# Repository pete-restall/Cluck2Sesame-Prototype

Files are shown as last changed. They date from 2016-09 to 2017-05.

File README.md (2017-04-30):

# Cluck<sup>2</sup>Sesame - Yet Another Chicken Coop Door Opener

## What is it ?
It opens and closes the door of my wife's chicken coop based on Sunrise and
Sunset times so that she doesn't have to.  Or rather, it will do when I get
the time to finish it between paid work and free time.

## Why 'Cluck<sup>2</sup>Sesame' ?
Because 'Cluck Cluck Sesame' is obviously what the chickens would say if
they needed to open a door.  And 'Chicken Sesame' is a recipe.

## The Hardware and Firmware
The hardware and firmware are all mine.  The board is based around a
[PIC16F685](doc/datasheets/mcu/PIC16F685-I.pdf) as I've had some lying around
for years and was looking for an excuse to use them up.

The PIC16F685 is an 8-bit microcontroller with a whopping 4K of program words
(flash) and 256 bytes of RAM that can run at a respectable 8MHz (2MIPS)
without an external clock.  But more importantly it's got excellent
power-saving capabilities, which is critical when running off batteries.
Being a PIC it's also got a brilliant array of peripherals and an adequate
20-pin package.

The firmware is an experiment in writing test-first assembler, an endeavour
somewhat trickier than with high-level counterparts due to its lack of
encapsulation, global state, side-effects, the vagaries of linking, as well
as the verbosity of the language.  The tests are run in gpsim with bash
scripts for glue.  They are run as part of the automated Travis build.

## Pictures
| Freshly baked and stuffed PCB         | Attached to the Coop                        |
----------------------------------------|----------------------------------------------
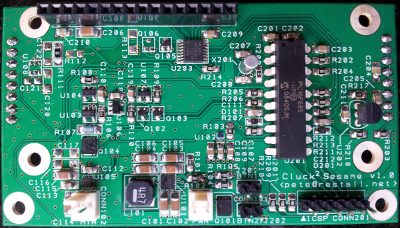
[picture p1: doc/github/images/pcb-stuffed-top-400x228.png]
Stuffed PCB
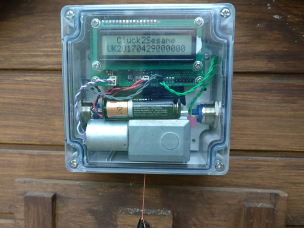
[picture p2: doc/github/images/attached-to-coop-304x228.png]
Attached to Coop
|  |  |

## Build


[stuffed-pcb-top-small]: doc/github/images/pcb-stuffed-top-400x228.png "Stuffed PCB (top)"
[attached-to-coop-small]: doc/github/images/attached-to-coop-304x228.png "Attached to Coop"

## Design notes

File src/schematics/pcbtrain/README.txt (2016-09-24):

Customer:
---------
Pete Restall (Parity Computer Consultancy Limited) - pete@restall.net
Any problems / questions, please do not hesitate to get in touch.

Guidelines Followed From:
-------------------------
http://www.pcbtrain.co.uk/schematic/pcb-technical-advice/

Design Tools Used:
------------------
DesignSpark 7.1
GC-Prevue 24.3.8

Track and Spacing:
------------------
Minimum 6mil.

Layers:
-------
All viewed from above, no mirroring.  Solder Resist layers are negatives, all
others are positives.  See "Cluck2Sesame Layers.pdf" for a non-Gerber
representation of what the individual layers should look like.

Board Outline:
--------------
All layers contain a zero-width board outline.  Outline size is
3.542in x 1.968in and >= 10mil from any feature, copper or otherwise.

Vias and Silkscreen:
--------------------
Some vias are partially covered with silkscreen; this is not anticipated to
be an issue since they should be covered / plugged with resist.

Pads and Silkscreen:
--------------------
CONN204 silkscreen touches the M3 washer pad in the top-left of the board but
should not cover it.  The silkscreen can be clipped where necessary, but
please advise if this is going to be an issue.

Vias and Pads:
--------------
Some vias are very close to pads, but the outer edge of drill holes should
be >= 6mil from the edge of the pad.  This may or may not be an issue (ie.
solder resist only covering part of a via), but please advise if it will
impact on manufacture.

There are two vias inside the thermal pad of U101.  These are not tented as
they provide thermal relief.  Please advise if this is an issue.

Drill Holes:
------------
All are through-plated and are finished sizes; no adjustments have been made
for plating thickness.  All are >= 10mil from the edge of the board.

Bit sizes can be rounded to the nearest 0.1mm.  Please advise if any drill
sizes are found to be incompatible with your processes.

Annular rings >= 6mil.

Data Formats:
-------------
More detailed information can be found in "DesignSpark Plot Report.TXT", but
in summary:

---------------
Gerber Settings
---------------

    Leading zero suppression.
    G01 assumed throughout.
    Line termination <*> <CR> <LF>.
    3.5 format absolute inches.
    Format commands defined in Gerber file.
    Aperture table defined in Gerber file.
    Hardware arcs allowed.

--------------
Drill Settings
--------------

    Excellon Format 1
    Format 3.5 absolute in inches.
    No zero suppression.

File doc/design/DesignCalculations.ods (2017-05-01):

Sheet: Motor
Lifting a Weight
Weight (kg) | 1
Height (cm) | 40
Time to Raise (s) | 20
Mechanical Power Required (W) | 0.1962
Motor |  |  | Rapid 37-0142 | JGY-370-320
Output Power (W) | 0.56 | Datasheet parameter | 0.56 | 0.45
Current (mA) | 360 | Datasheet parameter | 360 | 230
Angular Speed (rpm) | 5200 | Datasheet parameter | 5200 | 7
Torque (g.cm) | 10.5 | Datasheet parameter | 10.5 | 1000
Efficiency | 51.90% | Datasheet parameter | 51.90% | 30.00%
Input Power (W) | 1.07899807321773 | Worm efficiency will be < 50%, so add a decent margin; also allow higher transient current when starting (overcome worm static friction)
Angular Speed (rads/s) | 544.542726622231
Torque (Nm) | 0.00102969825315
Gears
Worm Gear Reduction (1:N) | 150
Shaft / Pulley Diameter (mm) | 20
Torque of 1kg Weight on Pulley (Nm) | 0.0981
Angular Speed (rpm) | 34.6666666666667
Angular Speed (rads/s) | 3.63028484414821
Torque at Worm Gear (Nm) | 0.1544547379725
Lifting Force (N) | 15.44547379725
Lifting Weight (kg) | 1.57446216077982
Lifting Speed (mm/s) | 36.3028484414821
Time to Raise (s) | 11.0184191371312
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

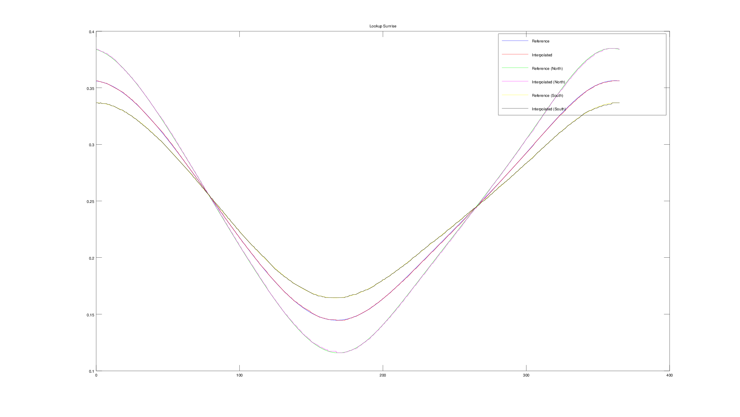
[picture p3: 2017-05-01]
doc/github/images/octave-sunrise-lookup-comparison-1920x1080.png

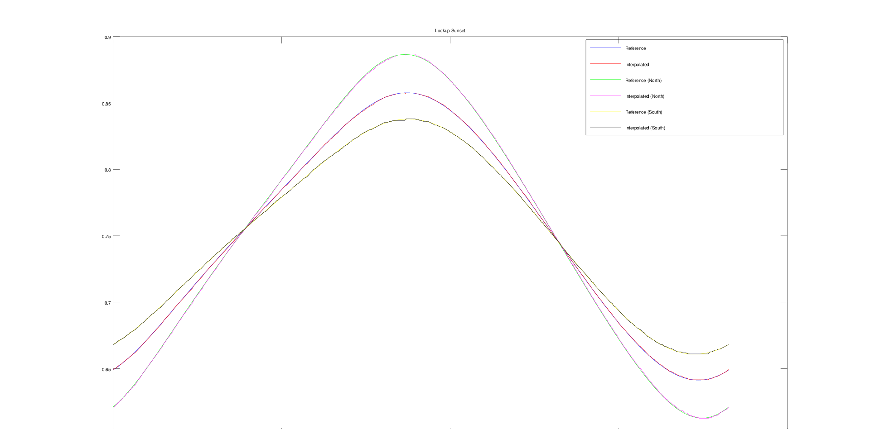
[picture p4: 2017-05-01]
doc/github/images/octave-sunset-lookup-comparison-1920x1080.png

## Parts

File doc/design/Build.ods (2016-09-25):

Item | Quantity Required | Quantity Bought | Total Cost | Cost per Unit
LCD | 1 | 2 | £9.54 | £4.77
Motor (With 1:150 Gearbox) | 1 | 1 | £9.20 | £9.20
PCB | 1 | 2 | £58.09 | £29.05
Paste Stencil | 1 | 1 | £14.34 | £14.34
Enclosure | 1 | 1 | £15.90 | £15.90
Buttons | 2 | 2 | £4.78 | £4.78
AA Battery Holders | 2 | 3 | £1.32 | £0.88
LCD Header (Board) | 1 | 10 | £1.74 | £0.17
LCD Header (LCD) | 1 | 10 | £2.75 | £0.28
Button Headers (Board) | 2 | 10 | £2.22 | £0.44
Button Headers (Cable) | 2 | 10 | £0.98 | £0.20
PIC ICSP Header | 1 | 1 | £0.00 | £0.00 | Off-cut from PCB Header
Power Header (Board) | 1 | 10 | £0.98 | £0.10
Power Header (Cable) | 1 | 10 | £0.54 | £0.05
Motor Header (Board) | 1 | 1 | £0.00 | £0.00 | Same as Button Headers
Motor Header (Cable) | 1 | 1 | £0.00 | £0.00 | Same as Power Header
Daughterboard Header | 2 | 10 | £1.03 | £0.21
 |  |  | £123.41 | £80.36

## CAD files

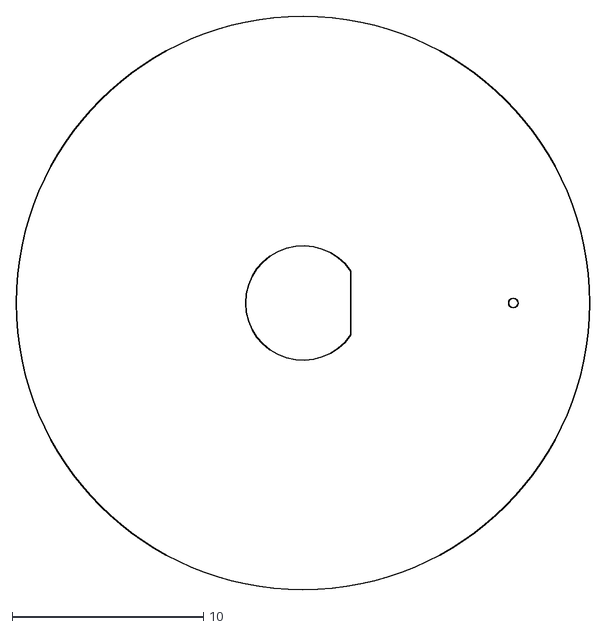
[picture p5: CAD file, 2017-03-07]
src/cnc/Spool/3-Spool.dxf
30.0 x 30.0

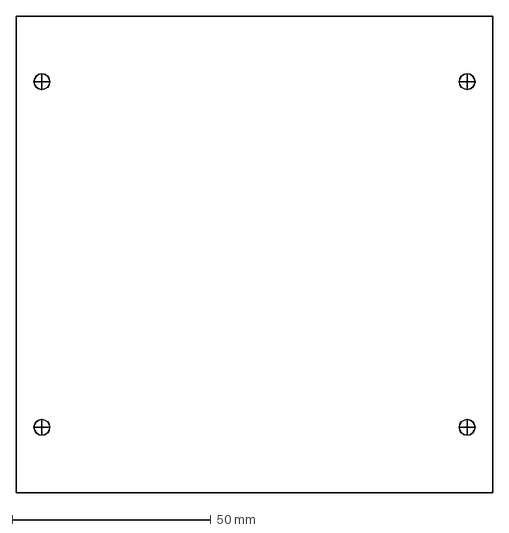
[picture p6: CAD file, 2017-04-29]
src/drawings/MountingHolesTemplate.dxf
120.0 x 120.0 mm

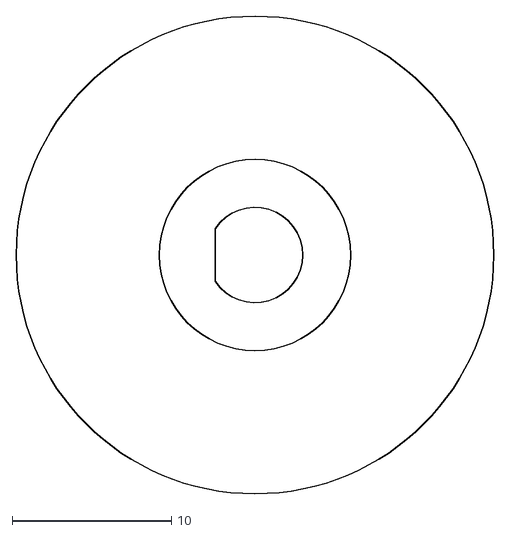
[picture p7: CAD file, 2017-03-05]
src/cnc/Spool/2-Spool.dxf
30.0 x 30.0

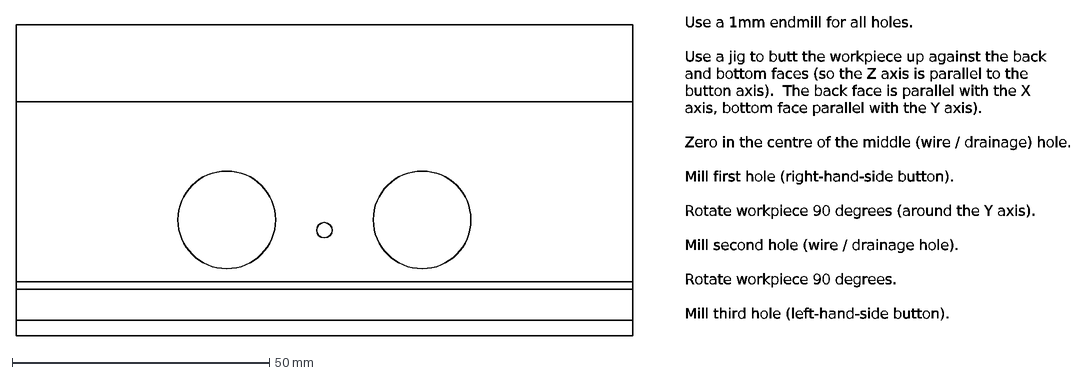
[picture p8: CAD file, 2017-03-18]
src/drawings/Enclosure.dxf
Use a 1mm endmill for all holes. Use a jig to butt the workpiece up against the back and bottom faces (so the Z axis is parallel to the button axis). The back f

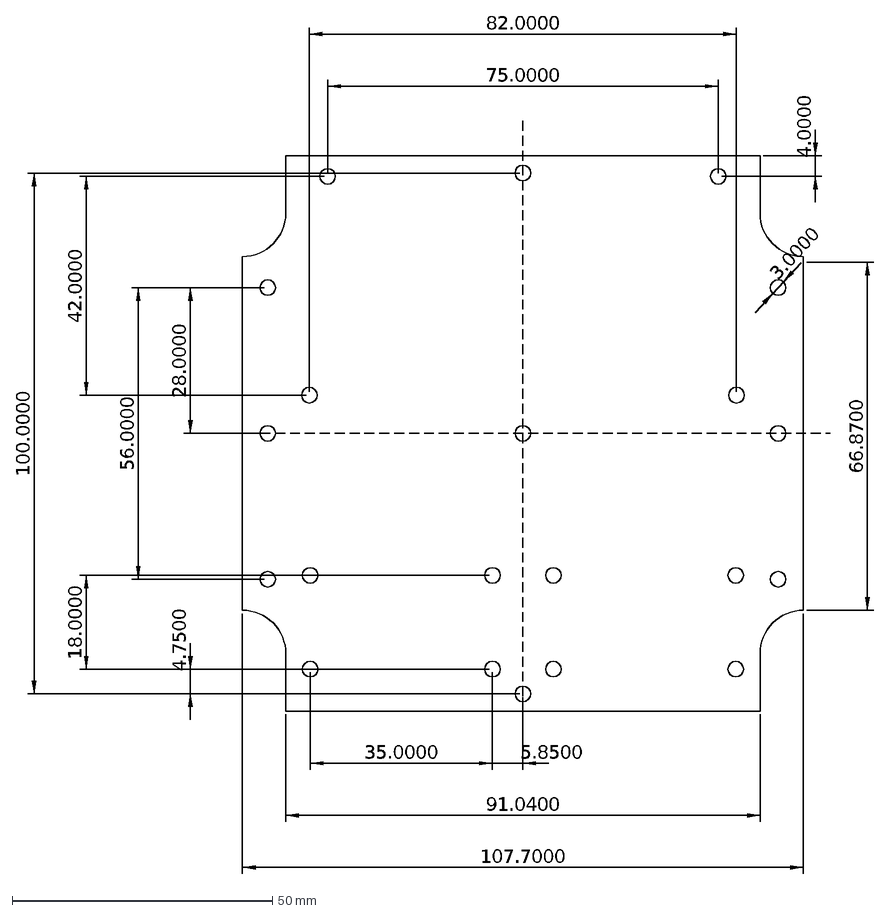
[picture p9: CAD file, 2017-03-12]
src/drawings/BackPlate.dxf
82.0000
4.0000
75.0000
3.0000
66.8700
28.0000
56.0000
42.0000
100.0000
107.7000
91.0400
5.8500
4.7500
18.0000
35.0000

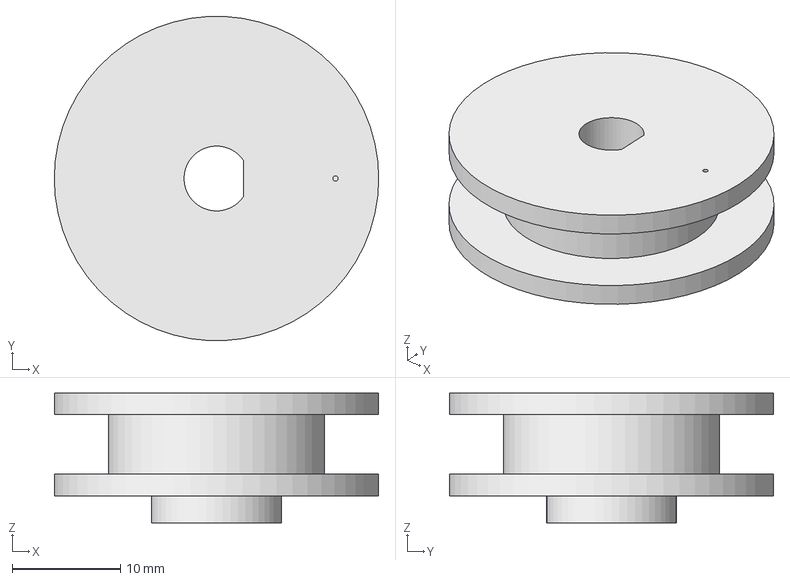
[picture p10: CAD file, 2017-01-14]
src/drawings/Spool.FCStd
30.0 x 30.0 x 12.0 mm

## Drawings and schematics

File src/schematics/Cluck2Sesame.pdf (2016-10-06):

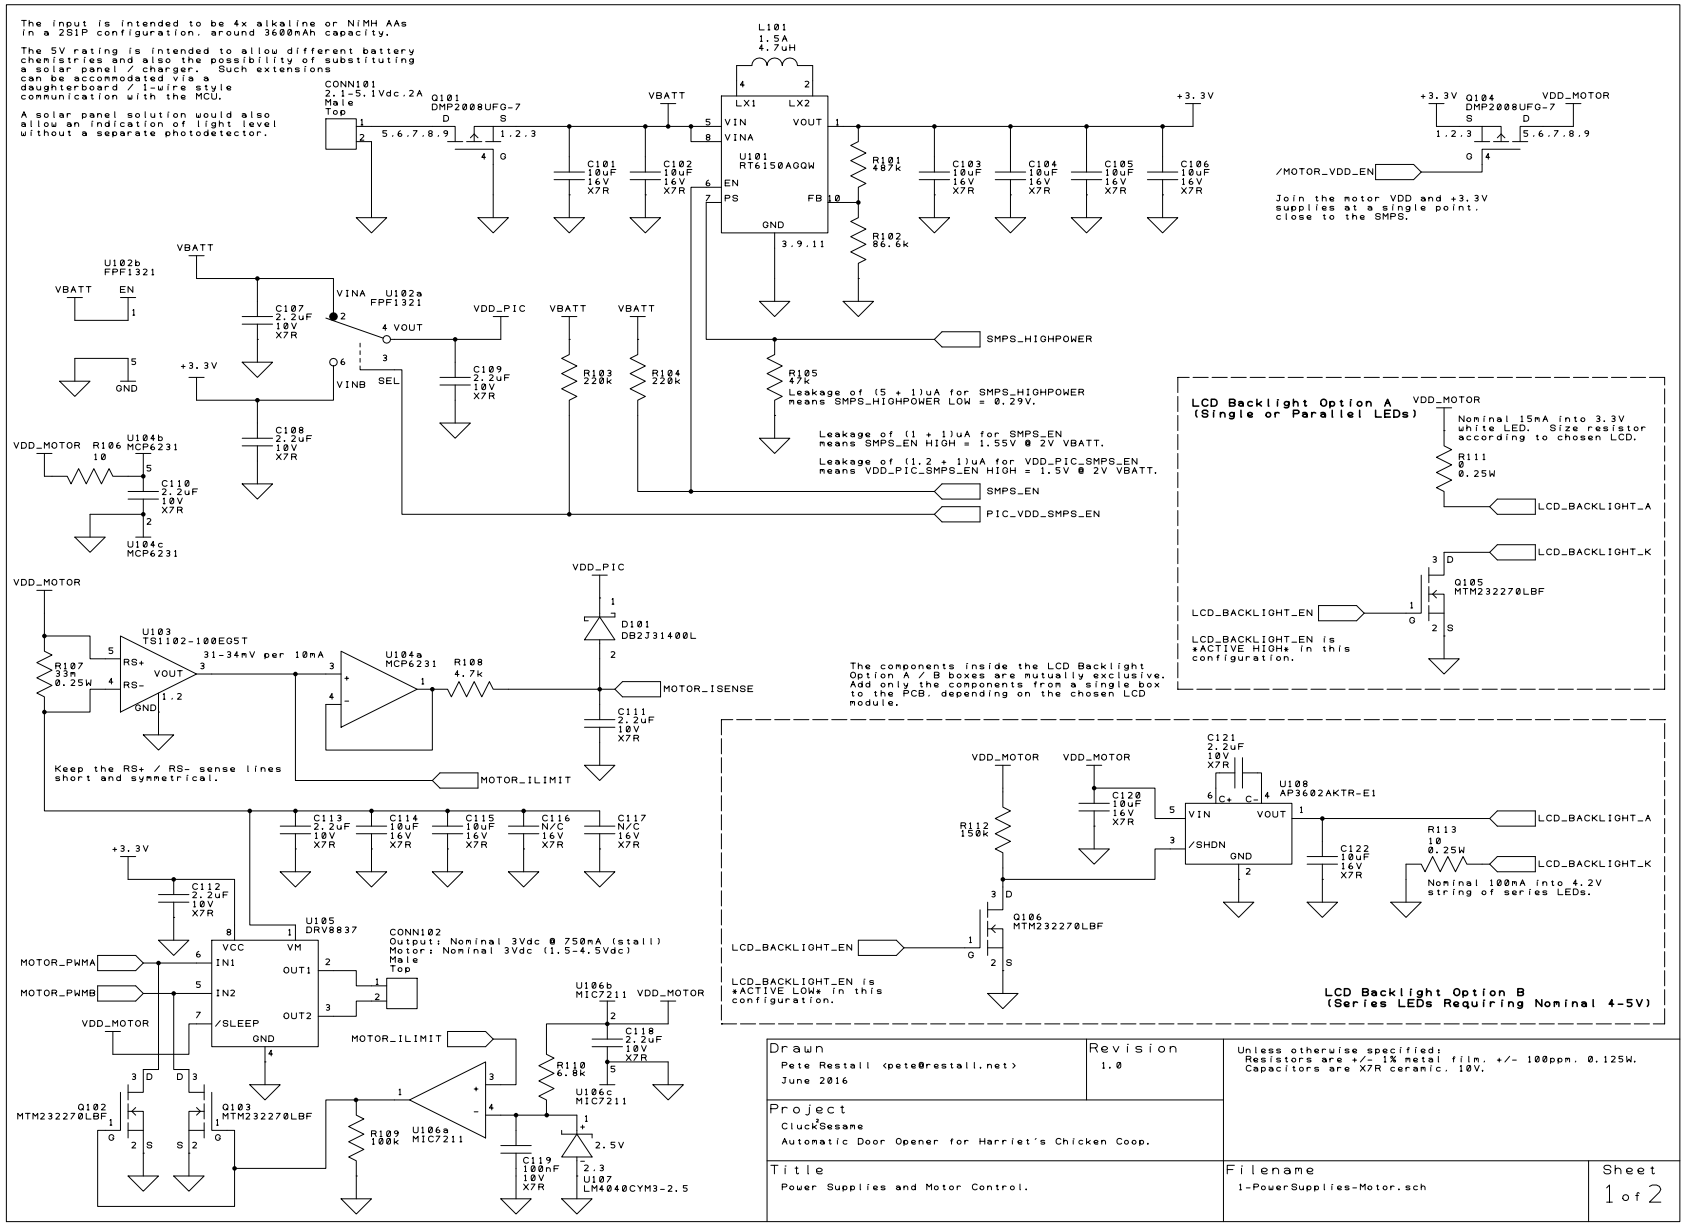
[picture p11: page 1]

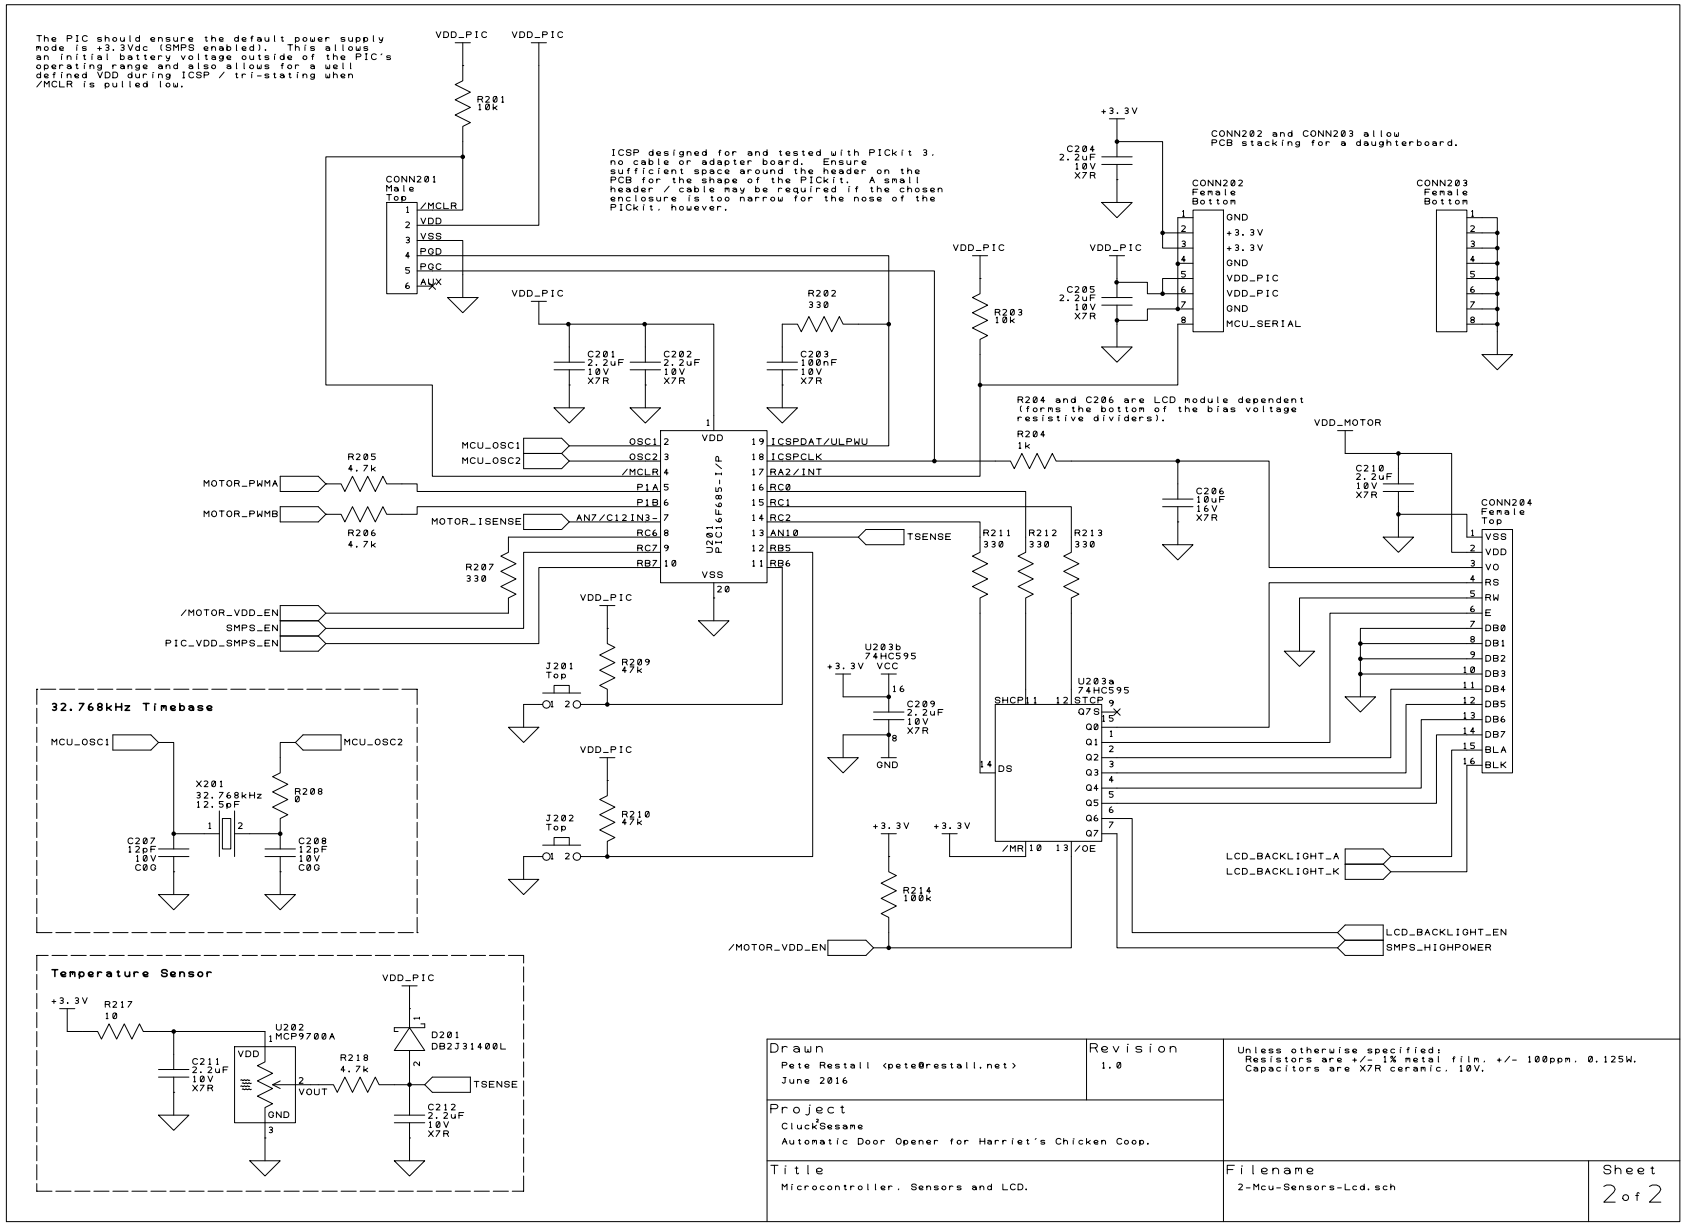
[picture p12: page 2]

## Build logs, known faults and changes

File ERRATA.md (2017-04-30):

# Cluck<sup>2</sup>Sesame - Yet Another Chicken Coop Door Opener
# Errata, Suggested Improvements and Otherwise Undocumented Design Changes

## PCB
- After testing with the actual motor, the LM4040CYM3-2.5 would be best
  replaced with a reference of 2V (or 2.048V for another LM4040 series) for
  a cut-off of about 600mA; the firmware cut-off is about 500mA.  Don't forget
  to re-calculate R110 for the new quiescent current !

- The PIC16F685 was really the wrong choice for this application, but it was
  chosen because it was lying around.  More program space would have eased
  the firmware constraints.  More pins would have allowed the shift register
  to be removed.

## Spool
- The tie-hole on the spool was increased from 0.5mm to 0.8mm to accomodate
  the multi-stranded line.  Multi-stranded line has less stretch and is a
  better fit for this application.

- The height of the stand-off for the spool was decreased as the width of the
  winding section was increased to 5mm.

## Motor
- The JGY-370 is a 6V motor running at around 3V.  While it is sufficient to
  raise and lower a door of about 500g, it wouldn't cope particularly well
  with the 1kg load that was the initial target weight.  Indeed, the current
  cut-off kicks in well before 1kg.

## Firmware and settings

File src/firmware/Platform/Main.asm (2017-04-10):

	#include "Platform.inc"
	#include "FarCalls.inc"
	#include "PowerOnReset.inc"
	#include "BrownOutReset.inc"
	#include "MclrReset.inc"
	#include "PowerManagement.inc"

	radix decimal

	extern pollForWork

Main code
	global main
	global initialisationCompleted

main:
	.safelySetBankFor PCON
	btfss PCON, NOT_POR
	goto powerOnReset
	btfss PCON, NOT_BOR
	goto brownOutReset

mclrReset:
	fcall initialiseAfterMclrReset
	goto pollingLoop

powerOnReset:
	fcall initialiseAfterPowerOnReset
	goto pollingLoop

brownOutReset:
	fcall initialiseAfterBrownOutReset

pollingLoop:
	fcall pollForWork
	goto pollingLoop

initialisationCompleted:
	.safelySetBankFor INTCON
	movlw (1 << GIE) | (1 << PEIE)
	iorwf INTCON

	fcall preventSleep
	fcall pollForWork
	fcall allowSlowClock
	return

	end

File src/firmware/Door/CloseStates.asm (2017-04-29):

	#include "Platform.inc"
	#include "FarCalls.inc"
	#include "Timer0.inc"
	#include "Motor.inc"
	#include "Door.inc"
	#include "States.inc"

	radix decimal

NUMBER_OF_TICKS_0_5S equ 2
NUMBER_OF_TICKS_5S equ 19
NUMBER_OF_TICKS_6S equ 23

	defineDoorState DOOR_STATE_CLOSE
		setDoorState DOOR_STATE_MOTORVDD_ENABLE
		setDoorNextState DOOR_STATE_CLOSE_MOTORVDDENABLED
		returnFromDoorState


	defineDoorStateInSameSection DOOR_STATE_CLOSE_MOTORVDDENABLED
		storeSlowTimer0 doorOperationStartedTimestamp

startLowering:
		.unknownBank
		setDoorState DOOR_STATE_MOTOR_STARTLOWERING
		setDoorNextState DOOR_STATE_CLOSE_LOWERING
		returnFromDoorState


	defineDoorStateInSameSection DOOR_STATE_CLOSE_LOWERING
		; TODO: OVERLOAD - FAULT
		; TODO: TIMEOUT - FAULT
		elapsedSinceSlowTimer0 doorTurnFullSpeedTimestamp
		sublw NUMBER_OF_TICKS_5S
		btfsc STATUS, C
		returnFromDoorState

rewindToTestMotorLoad:
		setDoorState DOOR_STATE_MOTOR_STARTRAISING
		setDoorNextState DOOR_STATE_CLOSE_RAISING
		returnFromDoorState


	defineDoorStateInSameSection DOOR_STATE_CLOSE_RAISING
		; TODO: OVERLOAD - FAULT
		; TODO: TIMEOUT - FAULT
		elapsedSinceSlowTimer0 doorTurnFullSpeedTimestamp
		sublw NUMBER_OF_TICKS_0_5S
		btfsc STATUS, C
		returnFromDoorState

ifMotorLoadPresentThenMoreLoweringIsRequired:
		.setBankFor motorFlags
		btfss motorFlags, MOTOR_FLAG_NOLOAD
		goto startLowering

loweredTooFar:
		bsf motorFlags, MOTOR_FLAG_PREVENT_NOMINALLOAD
		setDoorState DOOR_STATE_CLOSE_WAITFORISRSTOP
		returnFromDoorState


	defineDoorStateInSameSection DOOR_STATE_CLOSE_WAITFORISRSTOP
		.setBankFor PSTRCON
		movlw MOTOR_PSTRCON_OUTPUT_MASK
		andwf PSTRCON, W
		btfsc STATUS, Z
		goto motorStoppedByIsr

motorShouldNotRaiseMuchMoreThanItLowered:
		elapsedSinceSlowTimer0 doorTurnFullSpeedTimestamp
		sublw NUMBER_OF_TICKS_6S
		btfsc STATUS, C
		returnFromDoorState

		; TODO: TIMED OUT WHILE WAITING FOR LOAD TO BITE - FAULT

motorStoppedByIsr:
		.safelySetBankFor motorFlags
		bcf motorFlags, MOTOR_FLAG_PREVENT_NOMINALLOAD
		setDoorState DOOR_STATE_MOTOR_DONE
		setDoorNextState DOOR_STATE_CLOSED
		returnFromDoorState


	defineDoorStateInSameSection DOOR_STATE_CLOSED
		bsf doorFlags, DOOR_FLAG_CLOSED
		bcf doorFlags, DOOR_FLAG_OPENED
		setDoorState DOOR_STATE_WAIT_NEWDAY
		returnFromDoorState

	end

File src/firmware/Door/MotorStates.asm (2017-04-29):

	#include "Platform.inc"
	#include "FarCalls.inc"
	#include "Timer0.inc"
	#include "PowerManagement.inc"
	#include "Motor.inc"
	#include "Door.inc"
	#include "States.inc"

	radix decimal

	defineDoorState DOOR_STATE_MOTOR_STARTRAISING
		fcall turnMotorClockwise
		goto afterCallToTurn

	defineDoorStateInSameSection DOOR_STATE_MOTOR_STARTLOWERING
		fcall turnMotorAntiClockwise

afterCallToTurn:
		.unknownBank
		xorlw 0
		btfsc STATUS, Z
		returnFromDoorState

		storeSlowTimer0 doorTurnStartedTimestamp
		setDoorState DOOR_STATE_MOTOR_WAITFULLYTURNING
		returnFromDoorState


	defineDoorStateInSameSection DOOR_STATE_MOTOR_WAITFULLYTURNING
		fcall isMotorFullyTurning
		xorlw 0
		btfsc STATUS, Z
		returnFromDoorState

		storeSlowTimer0 doorTurnFullSpeedTimestamp

		.setBankFor doorNextState
		movf doorNextState, W
		movwf doorState
		returnFromDoorState


	defineDoorStateInSameSection DOOR_STATE_MOTOR_DONE
		fcall stopMotor
		setDoorState DOOR_STATE_MOTOR_WAITSTOP
		returnFromDoorState


	defineDoorStateInSameSection DOOR_STATE_MOTOR_WAITSTOP
		.setBankFor CCPR1L
		movf CCPR1L
		btfss STATUS, Z
		returnFromDoorState

		.setBankFor doorNextState
		movf doorNextState, W
		movwf doorState

		fcall disableMotorVdd
		fcall preventSleep
		returnFromDoorState

	end

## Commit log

2016-06-24 Initial commit.
    [1-PowerSupply.sch, 2-Microcontroller.sch, DesignCalculations.ods]
2016-06-24 The beginnings of an MCU schematic.
    [1-PowerSupply.sch, 2-Microcontroller.sch, DesignCalculations.ods]
2016-06-25 More work on the microcontroller schematics.
    [1-PowerSupply.sch, 2-Microcontroller.sch, DesignCalculations.ods]
2016-06-26 Started to add the sensors, LCD and headers.
    [1-PowerSupply.sch, 2-Mcu-Sensors-Lcd.sch, 2-Microcontroller.sch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]
2016-06-28 Started to think about the LCD backlight power supply and added to the power calculations.
    [1-PowerSupply.sch, 2-Mcu-Sensors-Lcd.sch, DesignCalculations.ods]
2016-06-30 Started looking at H-Bridges and motor power supply / control.
    [1-PowerSupply.sch, 2-Mcu-Sensors-Lcd.sch, DesignCalculations.ods]
2016-07-01 More motor driver calculations / schematics, plus started to keep a tab of material costs.
    [1-PowerSupply.sch, 2-Mcu-Sensors-Lcd.sch, Build.ods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]
2016-07-03 Filling in missing component values.
    [1-PowerSupplies-Motor.sch, 1-PowerSupply.sch, 2-Mcu-Sensors-Lcd.sch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]
2016-07-08 Various tidy-ups. Started to add a current limiter as the MCU won't be able to react quick enough before motor stall current pulls the VDD lines down.
    [1-PowerSupplies-Motor.sch, 2-Mcu-Sensors-Lcd.sch, DesignCalculations.ods]
2016-07-14 Removed the light sensor as it frees up another MCU pin for a dedicated VDD multiplexer (rather than sharing the SMPS enable line). This is pretty crucial, really (for switch-over timing). And the li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
    [1-PowerSupplies-Motor.sch, 2-Mcu-Sensors-Lcd.sch, DesignCalculations.ods]
2016-07-15 Started to create the component footprints.
    [1-PowerSupplies-Motor.sch, DesignCalculations.ods]
2016-07-19 Added the SOT23-5 footprint to the 1-PowerSupplies-Motor.sch components.
    [1-PowerSupplies-Motor.sch]
2016-07-20 Added the SOT23-3, SOT23-6, 6-WSON and 6-WLCSP footprints to the 1-PowerSupplies-Motor.sch components.
    [1-PowerSupplies-Motor.sch]
2016-07-30 Selected the enclosure. Added footprint for the LCD preset resistor.
    [1-PowerSupplies-Motor.sch, 2-Mcu-Sensors-Lcd.sch]
2016-07-31 Protection diodes for the PIC inputs when switching between power supplies. Various schematic tidy-ups. Added a button datasheet.
    [1-PowerSupplies-Motor.sch, 2-Mcu-Sensors-Lcd.sch, DesignCalculations.ods]
2016-08-05 Moved the motor driver from the +3.3V rail to the VDD_MOTOR rail; the extra drop should be neglegible and there are some power consumption gains. DesignCalculations.ods needs updating to reflect the 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
    [1-PowerSupplies-Motor.sch, 2-Mcu-Sensors-Lcd.sch, DesignCalculations.ods]
2016-08-07 Started work on the PCB.
    [1-PowerSupplies-Motor.sch, 2-Mcu-Sensors-Lcd.sch, DesignCalculations.ods]
2016-08-14 More PCB layout.
    [1-PowerSupplies-Motor.sch, 2-Mcu-Sensors-Lcd.sch]
2016-08-29 Most of the PCB routing is done, but in need of lots of tidy-ups once finalised. Removed some components to simplify the layout, including replacing the bulky pot with a Delta Sigma DAC for the LCD c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
    [1-PowerSupplies-Motor.sch, 2-Mcu-Sensors-Lcd.sch]
2016-09-04 PCB routing.
    [2-Mcu-Sensors-Lcd.sch]
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2016-09-16 PCB routing, pouring, DRC and silkscreen.
    [1-PowerSupplies-Motor.sch]
2016-09-18 Tweaks in order to finalise the PCB layout. Started to add the PCB Train build.
    [2-Mcu-Sensors-Lcd.sch]
2016-09-22 Removed thermal spokes from SMD pads and added them (manually...) to the TH parts - looks like DS doesn't differentiate pad types, unfortunately. More copper pour tweaking.
    [2-Mcu-Sensors-Lcd.sch]
2016-09-24 PCB layout completed and packaged for manufacture by PCB Train.
    [2-Mcu-Sensors-Lcd.sch, Build.ods]
2016-09-25 Removed board outline from top paste mask as submitted design to OSH Stencils for manufacture. Added some more components to the cost tally.
    [Build.ods]
2016-09-29 Started to add some gpsim testing infrastructure.
    [1-PowerSupplies-Motor.sch]
2016-10-02 Removed MPLABX support. Also missed some files from previous checkin.
    [Isr.asm, Main.asm]
2016-10-02 Added skeleton PowerOnReset, BrownOutReset and MclrReset tests.
2016-10-02 Added hook for the post-BOR/POR/MCLR reset initialisation chain.
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2016-10-08 Started to add some clock increment tests but realised gpsim stimuli are very limited / unflexible (dependent upon cycle counts, periodic / aperiodic but not a specific count of pulses for example). 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
2016-10-09 Added a load of include files for the modules (cleaner 'extern' handling). Started to add the Clock module tests / code. Fixed a bug with Arithmetic32 (incfsz does not affect the Z flag).
    [Main.asm]
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2016-10-16 Started to add the ShiftRegister module (and Motor module since it relies on MOTOR_VDD). Initialisation chain tests. Removed the '.done' macro for non-main() tests.
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2016-10-23 Added a Timer0 module and a simple way of determining an elapsed number of ticks.
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2016-10-23 The TemperatureSensor module is now wired into the initialisation and polling loops.
2016-10-23 Added TODOs for a couple of PORT RMW bugs.
2016-10-25 Added motor VDD enable / disable tests using pull-ups to verify RMW behaviour.
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2016-10-30 Fixed assertion bugs - gpsim assertions work off the current bank, so cross-bank assertions can't be used. This fix can be tidied up more with dedicated .assertEqual style macros, which are now possi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
2016-11-13 Added PreventInfiniteLoops.sti to all tests to prevent them hanging. LCD contrast, enableLcd(), disableLcd() and isLcdEnabled() now work as they should.
    [Initialise.asm, Isr.asm]
2016-11-13 Re-ordered the linked libraries in the utilities Makefiles to avoid the link error in Travis.
    [Isr.asm]
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2016-11-27 Added shift register initialisation to the LCD initialisation to prevent glitches on power-up.
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2016-12-04 An initial pollForWork() is now done after initialisation to allow any post-initialisation activities to prevent entering the (MCU) low-power mode by default.
    [Main.asm]
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2016-12-11 Started to play with Sunrise / Sunset algorithms.
    [DesignCalculations.ods]
2017-01-02 Fixed Julian date calculation (J2000 Epoch is midday, not midnight).
    [DesignCalculations.ods]
2017-01-13 Started the drawing for the spool.
    [Spool.FCStd]
2017-01-14 Additions to the spool drawing. I've abandoned the idea of a 2D orthographic projection since the FreeCAD functionality just isn't there - dimensions, for example, are abysmal. You can't even zoom in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
    [Spool.FCStd]
2017-01-30 Added a dayOfYear counter to the Clock module. Now clearing the date and time for non-Brown-Out Resets.
    [Initialise.asm]
2017-01-30 The ISR now prevents sleep for a single iteration of the polling loop, which gives the pollers an opportunity to process the output of the ISR if it occurs in the instruction immediately prior to the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
    [Isr.asm]
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2017-03-05 Added 2-Spool.nc, the gcode for milling the second half of the spool. Also added the Estlcam files that allow the generation of that gcode.
    [2-Spool.dxf]
2017-03-07 Added 3-SpoolFixture.nc and 3-Spool.nc, the final steps in the process of machining the spool. Plus Estlcam project and other support files.
    [3-Spool.dxf]
2017-03-12 Added the BackPlate drawing, Estlcam project and gcode.
    [BackPlate.dxf]
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2017-03-18 Added the Enclosure drawing, Estlcam project and gcode.
    [Enclosure.dxf]
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2017-03-24 Added randomised RAM contents to the tests to better replicate the real-world. This caught a couple of uses of uninitialised variables, which have been fixed.
    [Initialise.asm]
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2017-03-26 Added soft stop and reversal for the motor.
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2017-03-26 Added pulse steering for motor reversals.
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2017-03-29 Added ISR condition to monitor the motor current only if the channel is correct.
    [Isr.asm]
2017-03-30 Added motorStop() and optimised the soft start and stop algorithm (shortened in both time and space).
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2017-04-01 Brought Timer 2 under the control of the enableMotorVdd() and disableMotorVdd() functions. Bug fixed in the pulse steering tests.
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2017-04-09 Bugfix for the bank tracking. Added buttons and LCD backlight indicator to the testbench (properly).
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2017-04-09 Added motor indicators to the testbench. Fixed a bug (squashed carry bit) with the motor direction control in the turnMotor*Clockwise() functions. Added some overly simple up / down controls to the U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
2017-04-11 Added a button press timeout of 10 seconds to the non-settings screens of the UI. Once the power management is handled correctly, this lack of hooman interaction will enable the device to drop into a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
    [Initialise.asm]
2017-04-13 Initial motorFlags bugfix.
2017-04-16 Added the SMPS_HIGHPOWER assertion whenever enableMotorVdd() is called, plus increased the motor soft start time. This stops the VDD droop / glitch (to about 2.7V) that looks like a current surge (AD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
    [Initialise.asm]
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2017-04-29 Build fix - modified the gpsim patches to better reflect the current state of their trunk. The clock-switching still doesn't work, however.
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2017-04-29 Added a simple drill template for use when mounting the box to the coop.
    [MountingHolesTemplate.dxf]
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2017-05-01 Added a (UK) Daylight Savings Time algorithm and wired it into the Sunrise / Sunset calculations. The Clock module still needs to adjust for Daylight Savings Time, however.
    [DesignCalculations.ods]
2017-05-13 Bugfix for the button IOC; if a button was pressed during sleep then the device would only wake at the next clock tick and not immediately as expected..
    [Isr.asm]
